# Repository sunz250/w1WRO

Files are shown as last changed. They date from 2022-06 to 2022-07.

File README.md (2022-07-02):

РРО: Будущие инженеры 2022 | LigaRobotov_OSError
====

В репозитории содержатся инженерные материалы, созданные и использованные командой OSError при проектировании и программировании беспилотного автомобиля для участия в Российской робототехнической олимпиаде 2022 в категории Будущие инженеры.

__https://youtu.be/0HV11u2FUfQ  - URL-адрес видеоролика на платформе youtube, показывающий автономное вождение автомобиля и его краткий обзор__

## Содержание

* `team_photo` - 2 командные фотографии: одна официальная и одна неофициальная (забавная) со всеми членами команды
* `robot_photo` - 6 фотографий транспортного средства (со всех сторон, сверху и снизу)
* `Видео` - файл video.md, в котором содержится URL-адрес на видеоролик на платформе youtube, показывающий автономное вождение автомобиля и демонстрацию его отдельных компонентов 
* `schematic`- схематические диаграммы всеx электромеханических компонентов (электронные компоненты и двигатели), используемых в автомобиле, и способы их соединения друг с другом
* `src` - программный код беспилотного автомобиля.
* `3D модели` - 3D модели для печати, необходимые для производства элементов автомобиля

## Описание робота

  Наш робот создан для решения задания РРО категории Будущие Инженеры. Его главной задачей является прохождение гоночной трассы с установленными на ней дорожными знаками или смещенными коридорами на время. Дорожные знаки указывают сторону полосы движения, по которой должен следовать автомобиль. Если на пути красный столб - нужно держаться правой стороны полосы. Если зелёный, то левой стороны полосы. Задание считается выполненным, если автомобиль проехал 3 круга. Сбивать или сдвигать с места дорожные знаки - запрещено. Направление, в котором автомобиль должен двигаться по трассе (по часовой стрелке или против часовой стрелки), будет варьироваться в разных матчах. Начальное положение автомобиля, а также количество и расположение дорожных знаков определяются случайным образом во время жеребьёвки перед матчем.

  Для движения интеллектуального беспилотного автомобиля используется мотор на 600 оборотов в минуту и потребляющий напряжение в 12 Вольт, соединенный с ведущей осью через дифференциал. Такая конструкция позволяет равномерно распределять крутящий момент мотора между ведущими колесами и обеспечивает надлежащую плавность хода. 
  
  Для ориентирования в процессе движения по гоночной трассе наш робот оборудован всеми необходимыми датчиками и сенсорами, а также камерой. Среди них - датчик абсолютной ориентации BNO085. В BNO085 есть свой модуль вычислений, это 32-битное ядро ARM Cortex M0, что позволяет производить большинство расчетов непосредственно внутри BNO085 и пользоваться уже готовыми результатами. Ядро получает данные: акселерометра, гироскопа, магнитометра, производит расчеты и сохраняет результаты. Результаты в дальнейшем могут быть запрошены внешними устройствами. 

  Для определения цвета дорожных знаков и ориентации используются 2 камеры, оснащенные сенсором SONY IMX-477, подключаются через интерфейс CSI.
  
  Главным вычислительным модулем на роботе является одноплатный вычислительный модуль NVIDIA Jetson Nano. Модуль Jetson Nano — это компактный компьютер на базе ИИ, который обладает производительностью и энергоэффективностью, необходимой для современных задач искусственного интеллекта, параллельной работы нескольких нейронных сетей и одновременной обработки данных с нескольких датчиков высокого разрешения. Поэтому он представляет собой отличное начальное решение для внедрения сложных средств искусственного интеллекта во встраиваемые системы. NVIDIA Jetson Nano обеспечивает потрясающие новые возможности в миллионах компактных энергоэффективных систем ИИ. Решение открывает новые возможности для встроенных IoT-приложений, в том числе для видеорегистраторов начального уровня, домашних роботов и интеллектуальных шлюзов с возможностями аналитики. 

## Описание алгоритма

  Для __квалификационного__ этапа соревнований используется программа cvalification.py. Стратегия прохождения данного этапа – движение вдоль внешней черной стены, используя показания BNO, те придерживаясь курса. После запуска программа инициализирует все необходимые модули, зажигается синий светодиод – робот готов к старту, необходимо лишь нажать кнопку. Далее робот набирает крейсерскую скорость и едет до ближайшей цветной линии. Если линия синего цвета – движение против часовой стрелки, если оранжевого – наоборот. Как только направление движения распознано, задается значение переменной clock: 1 по часовой и -1 против, она будет использоваться при расчете курса BNO. Далее движение продолжается до того, как робот увидит стену впереди себя, после чего требуемый курс BNO меняется на 90 градусов влево или вправо в зависимости от направления движения. Как только робот поворачивает, к счетчику секторов прибавляется 1. Так после 3х кругов, когда значение счетчика равно 12, робот останавливается.

  Для __финального__ этапа соревнований используется программа final.py. По большей части она аналогична cvalification.py, но также добавлено распознавание дорожных знаков. Старт, финиш и определение направление движения происходят как на квалификации. В поворотах объезд кубиков производится по пропорционально-дифференциальному регулятору, как только робот замечает кубик и определяет его цвет и позицию – начинается регуляция, причем различная в зависимости от положения знака. На прямых участках трассы регулирование реализовано иначе: используя метод векторов, робот рассчитывает угол отклонения знака от траектории движения, после чего рассчитывает ошибку в зависимости от цвета и положения кубика, своего положения, отклонения от курса, величины угла отклонения знака, которая корректирует курс BNO. Используя функциональную зависимость, калькулируется время маневра, после чего робот меняет свой курс, объезжая знак или приближаясь к нему, в конце маневра возвращаясь на исходную прямую траекторию. 

## Инструкция по сборке автомобиля

__1.	Начинаем с нижней рамы и крепления сервомотора__

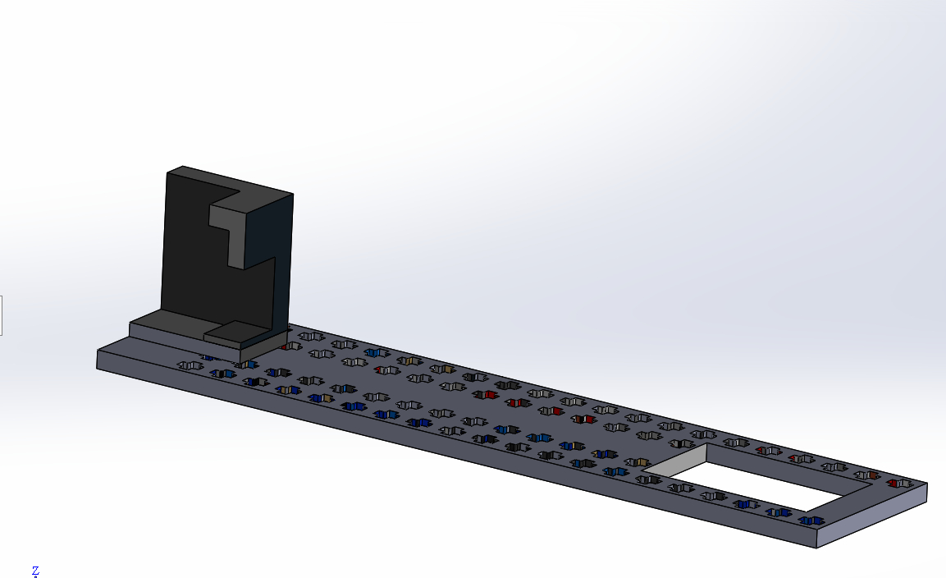
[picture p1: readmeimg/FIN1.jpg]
FIN1


__2.	Устанавливаем штифты и оси LEGO для крепления других элементов__

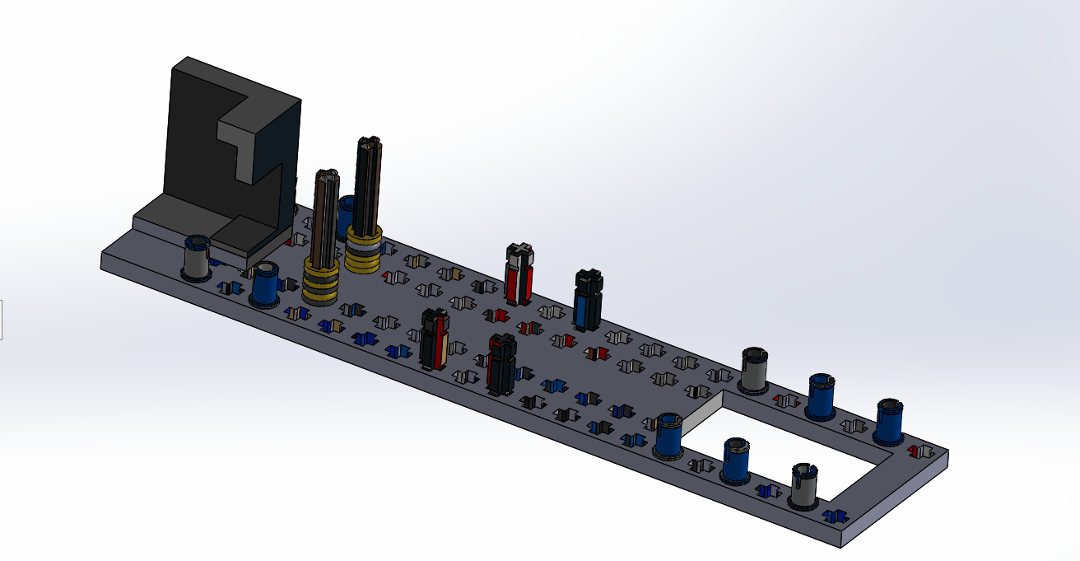
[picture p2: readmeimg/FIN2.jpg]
FIN2


__3.	Устанавливаем балки LEGO__

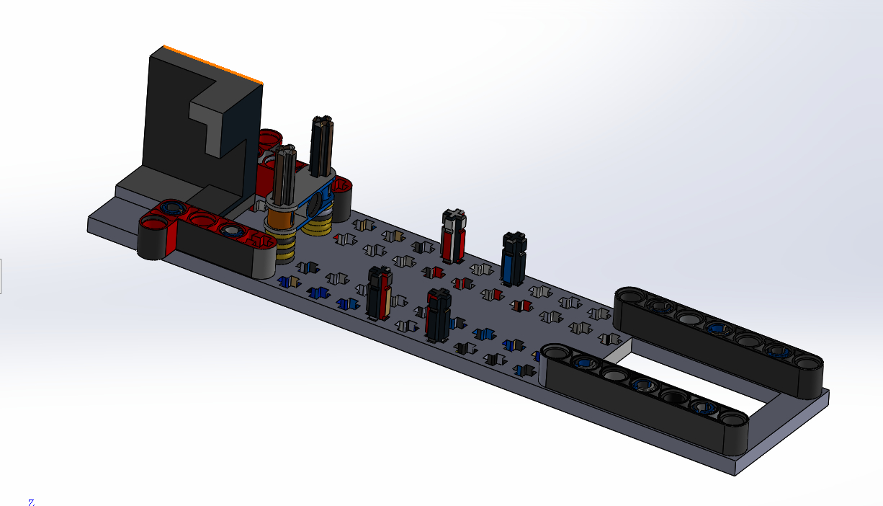
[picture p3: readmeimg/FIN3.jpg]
FIN3


__4.	Устанавливаем сервомотор__

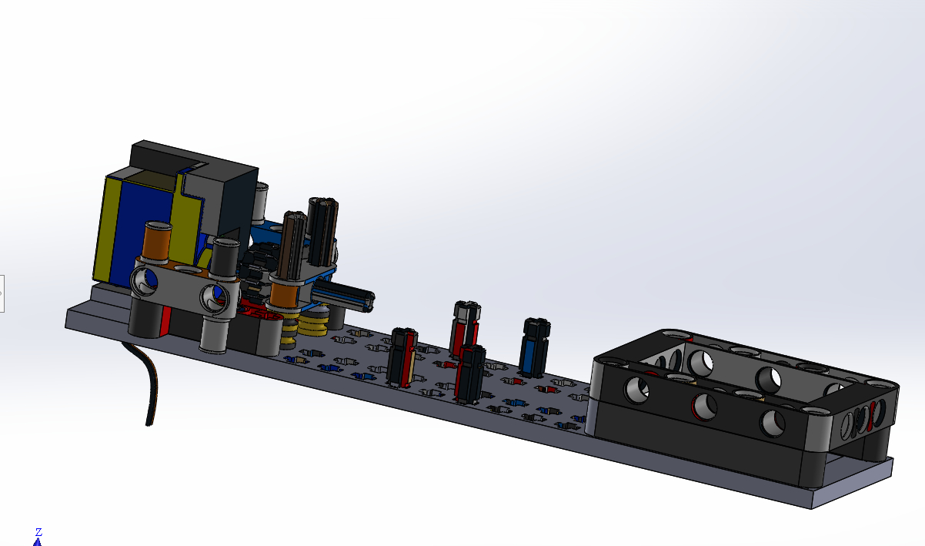
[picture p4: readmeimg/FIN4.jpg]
FIN4


__5.	Устанавливаем элементы рулевой рейки и дифференциал__

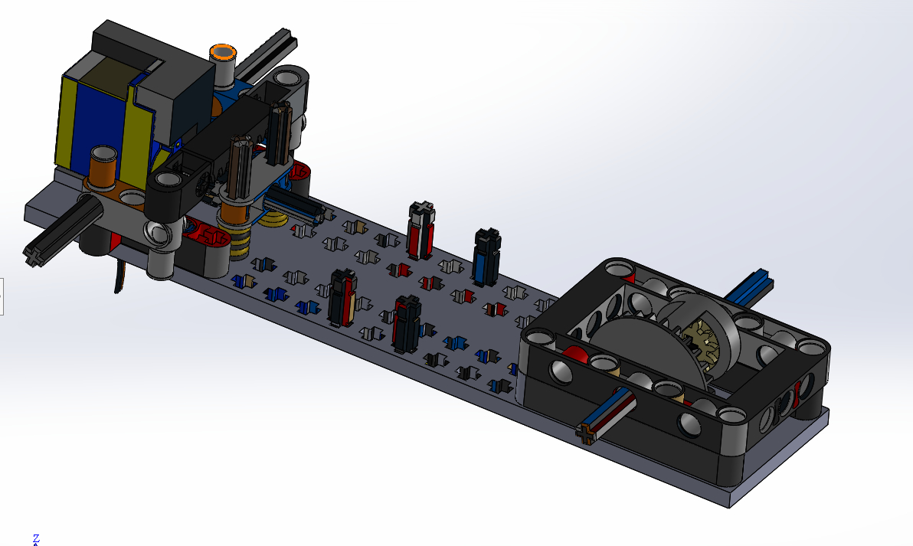
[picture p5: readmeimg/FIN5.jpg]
FIN5


__6.	Втыкаем LEGO штифты __

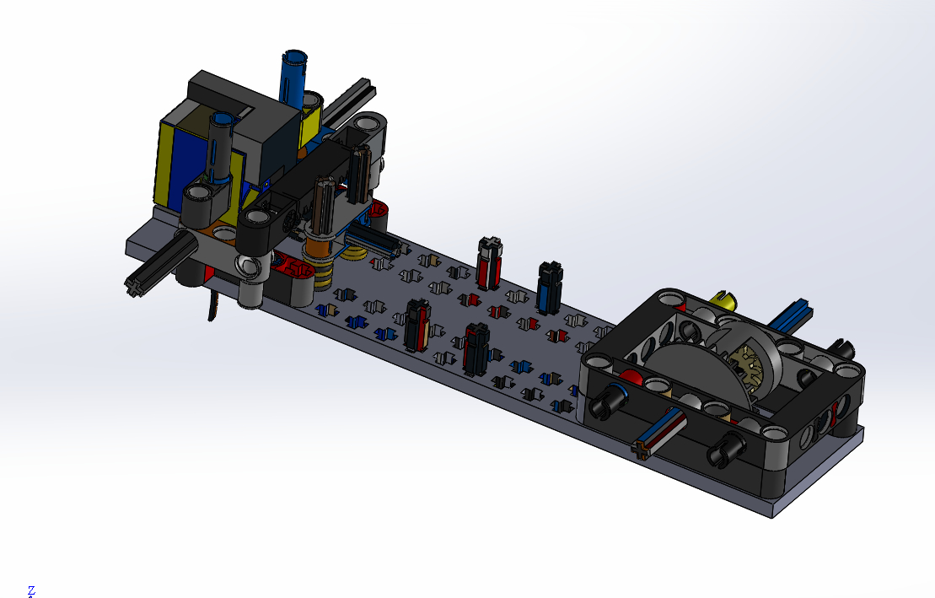
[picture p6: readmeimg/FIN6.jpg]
FIN6


__7.	Устанавливаем уголки и балки LEGO__

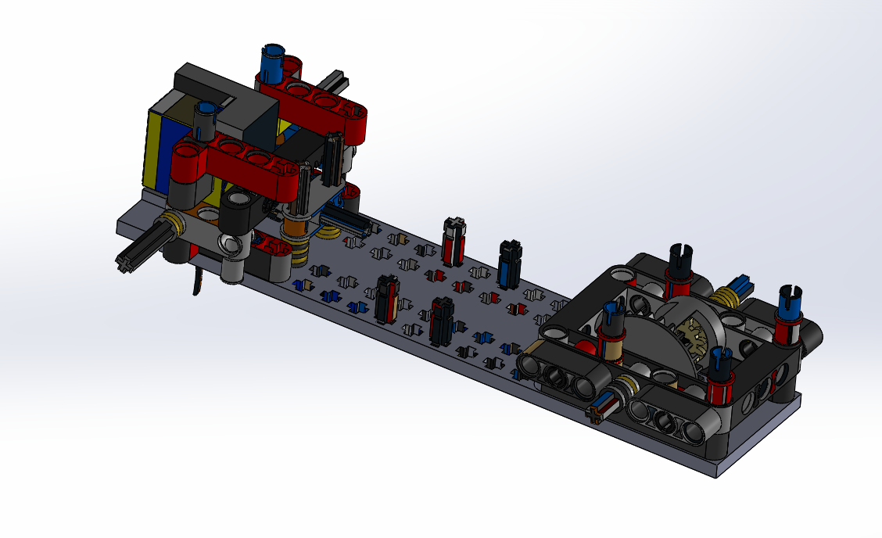
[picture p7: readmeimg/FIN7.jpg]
FIN7


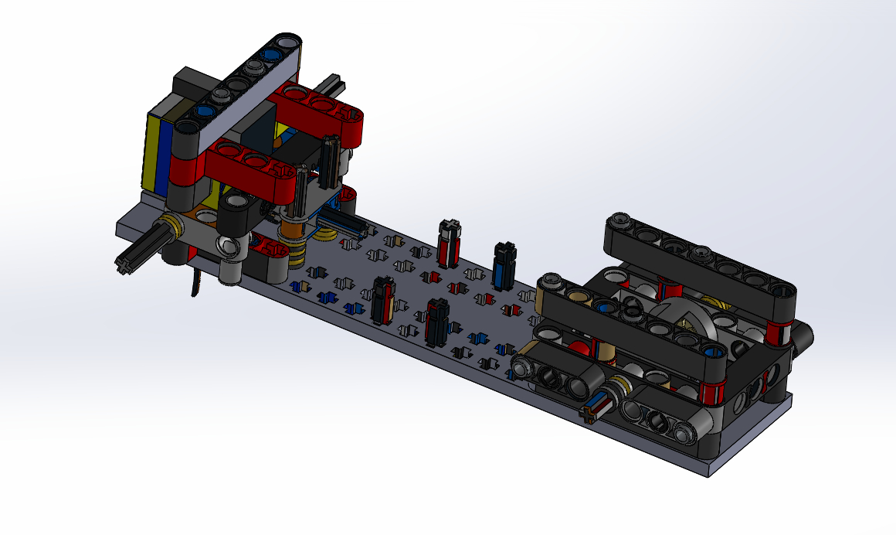
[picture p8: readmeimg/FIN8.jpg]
FIN8


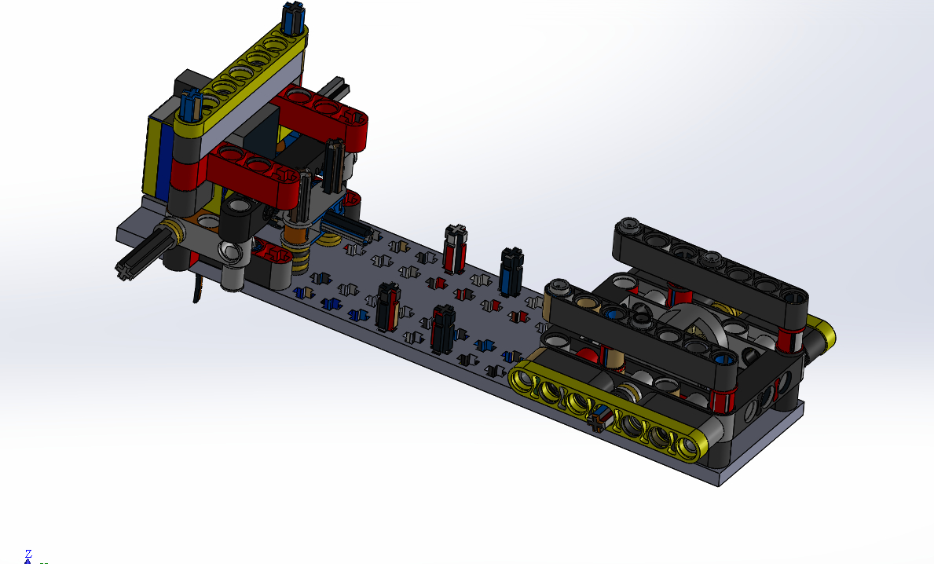
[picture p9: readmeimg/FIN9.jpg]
FIN9


__8.	Устанавливаем блок с мотором__

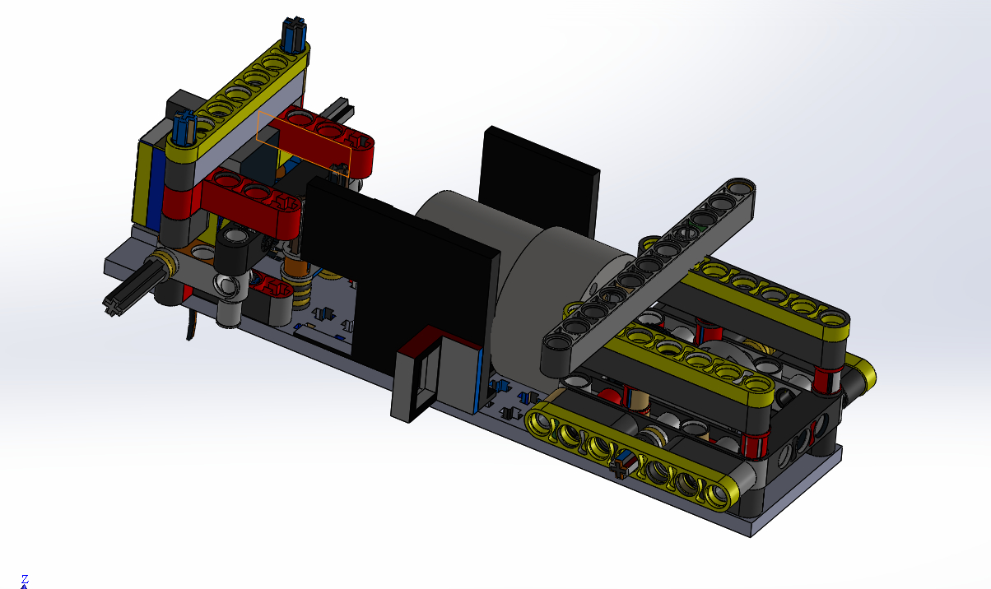
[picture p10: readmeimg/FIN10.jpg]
FIN10


__9.	Устанавливаем крепление JETSON NANO__

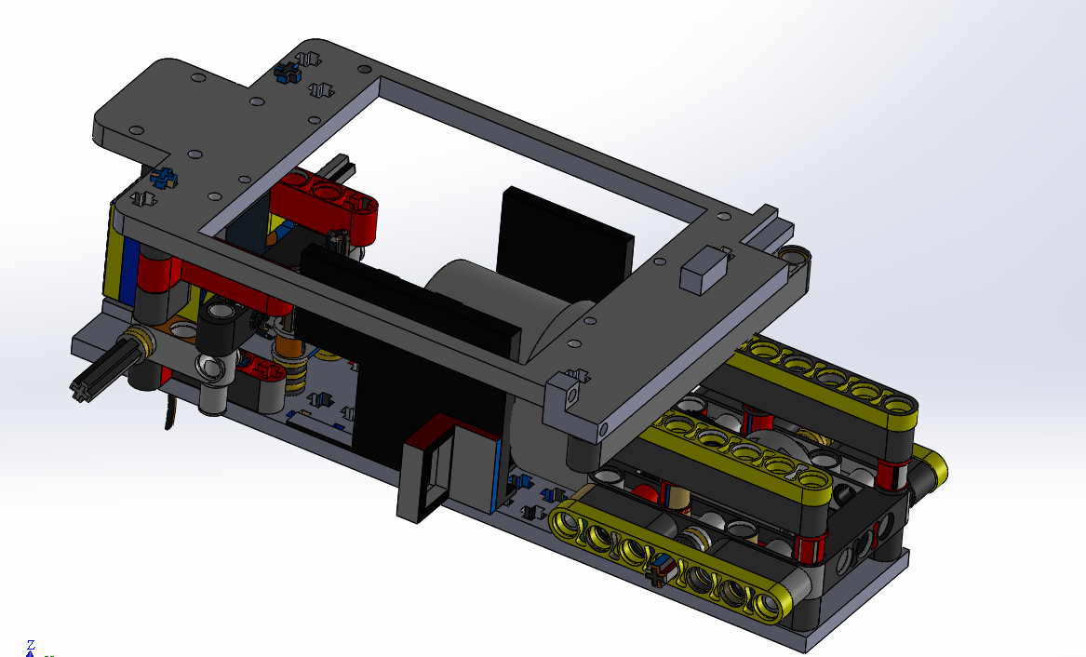
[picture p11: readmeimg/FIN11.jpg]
FIN11


__10.	Устанавливаем UPS POWER MODULE для JETSON NANO__

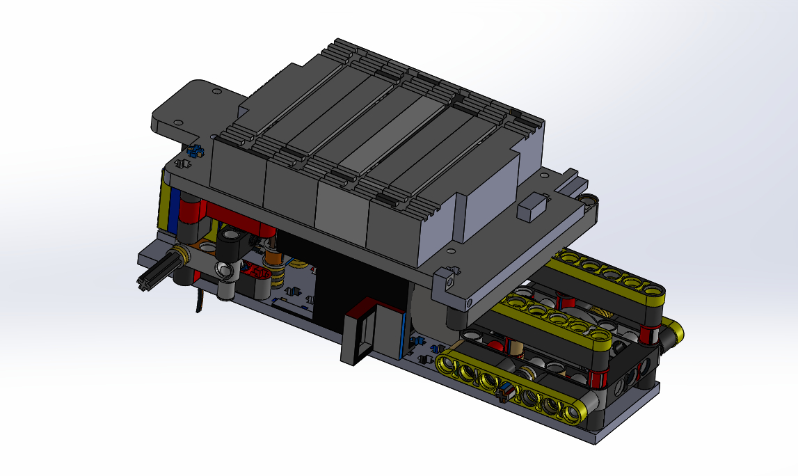
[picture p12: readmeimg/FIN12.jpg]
FIN12


__11.	Устанавливаем колеса__

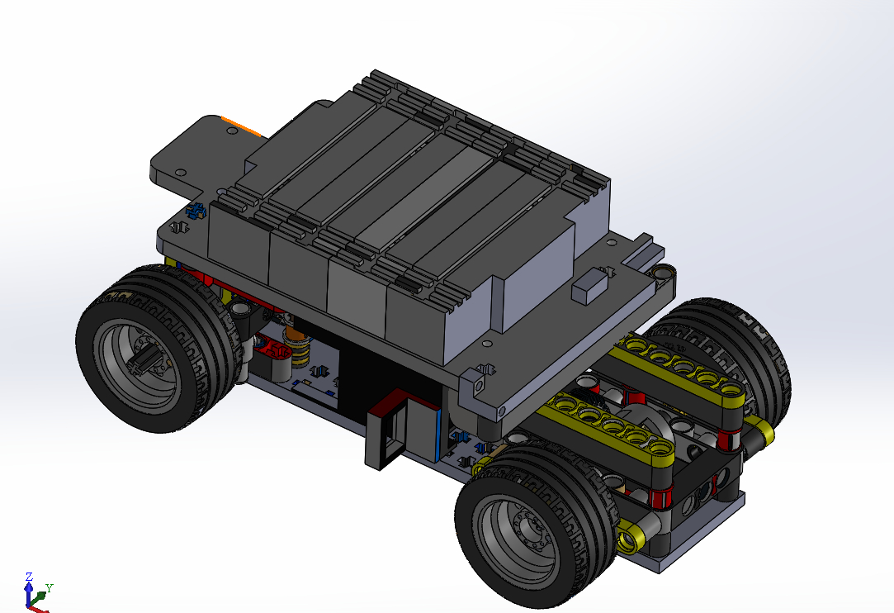
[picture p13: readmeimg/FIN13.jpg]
FIN13


__12.	Устанавливаем servo shield__

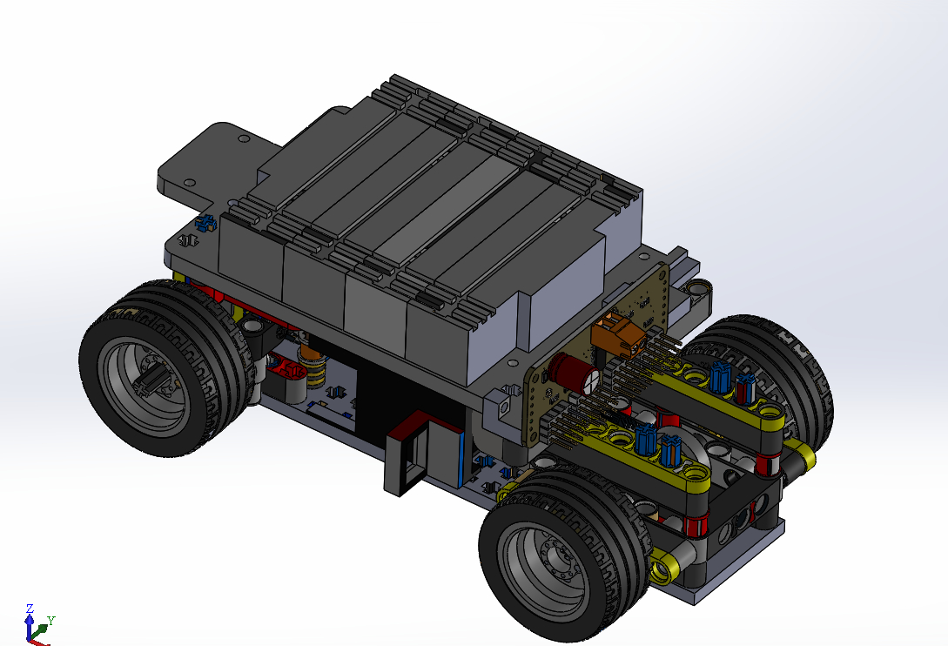
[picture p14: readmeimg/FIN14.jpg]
FIN14


__13.	Устанавливаем крепление камер и сами камеры, батарейный блок для мотора__

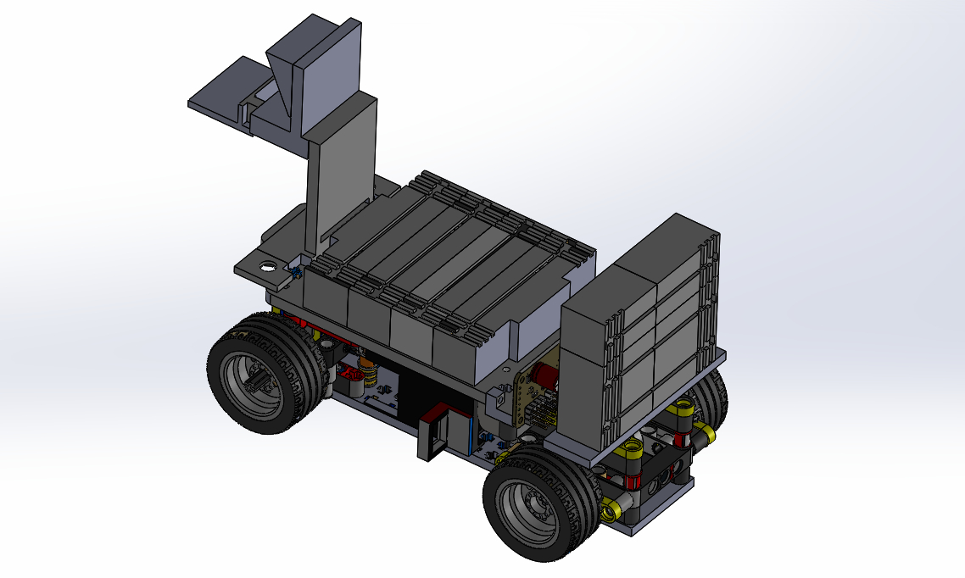
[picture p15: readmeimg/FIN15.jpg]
FIN15


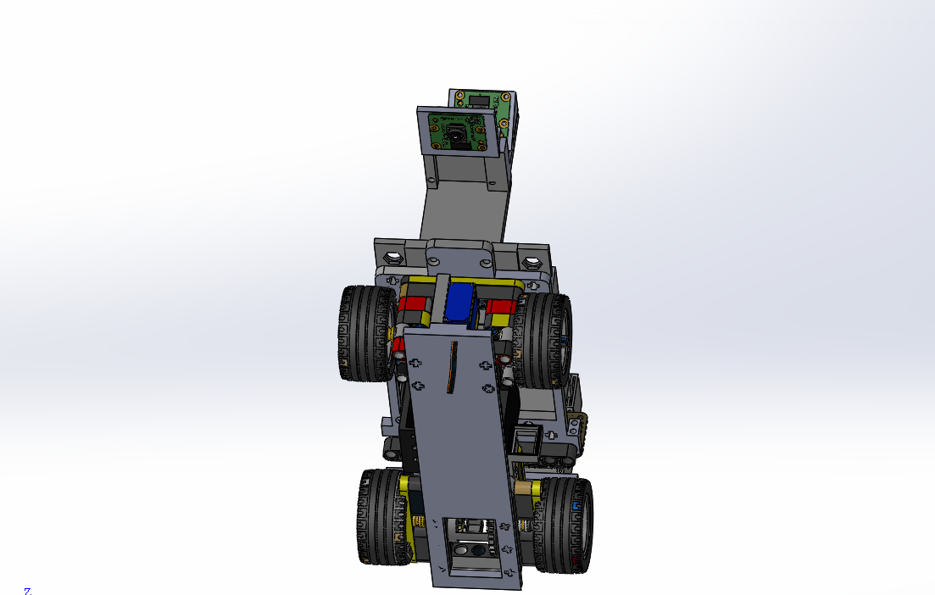
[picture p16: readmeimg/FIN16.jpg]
FIN16


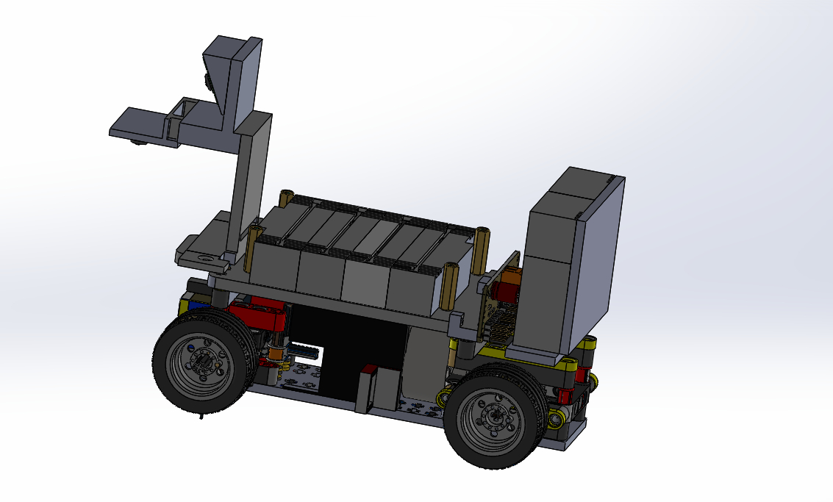
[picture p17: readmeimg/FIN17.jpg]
FIN17


__14.	Устанавливаем JETSON NANO, верхний блок с кнопкой, светодиодами, датчиком BNO085, DC-DC преобразователь для питания мотора, антенны (при необходимости). Сборка готова__

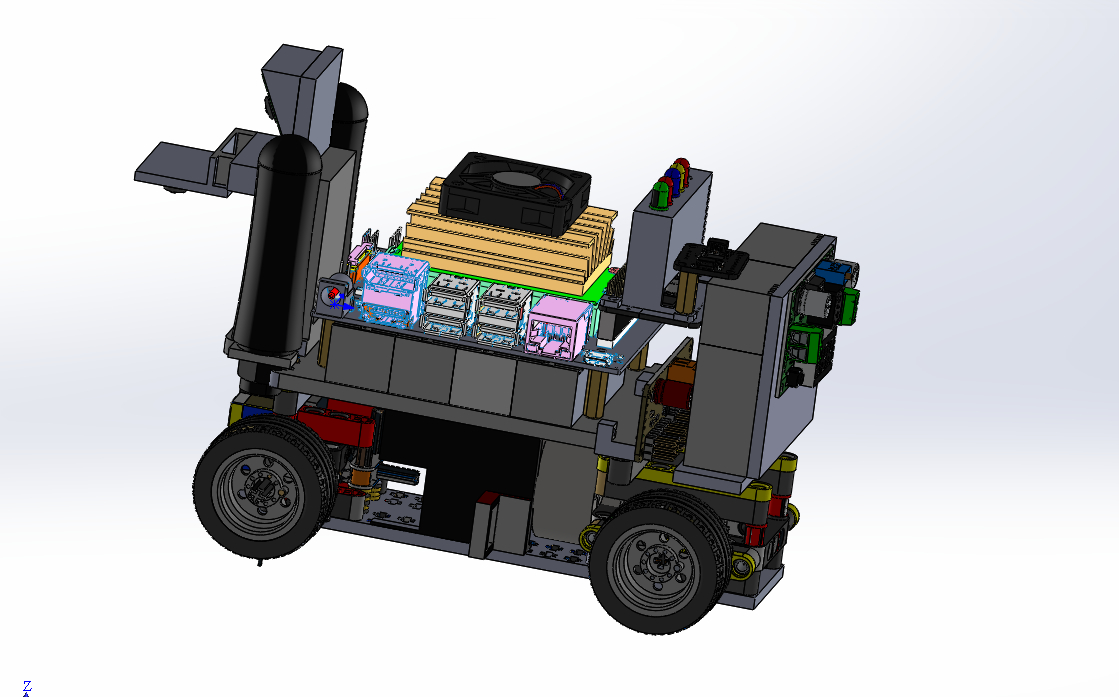
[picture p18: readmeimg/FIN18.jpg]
FIN18


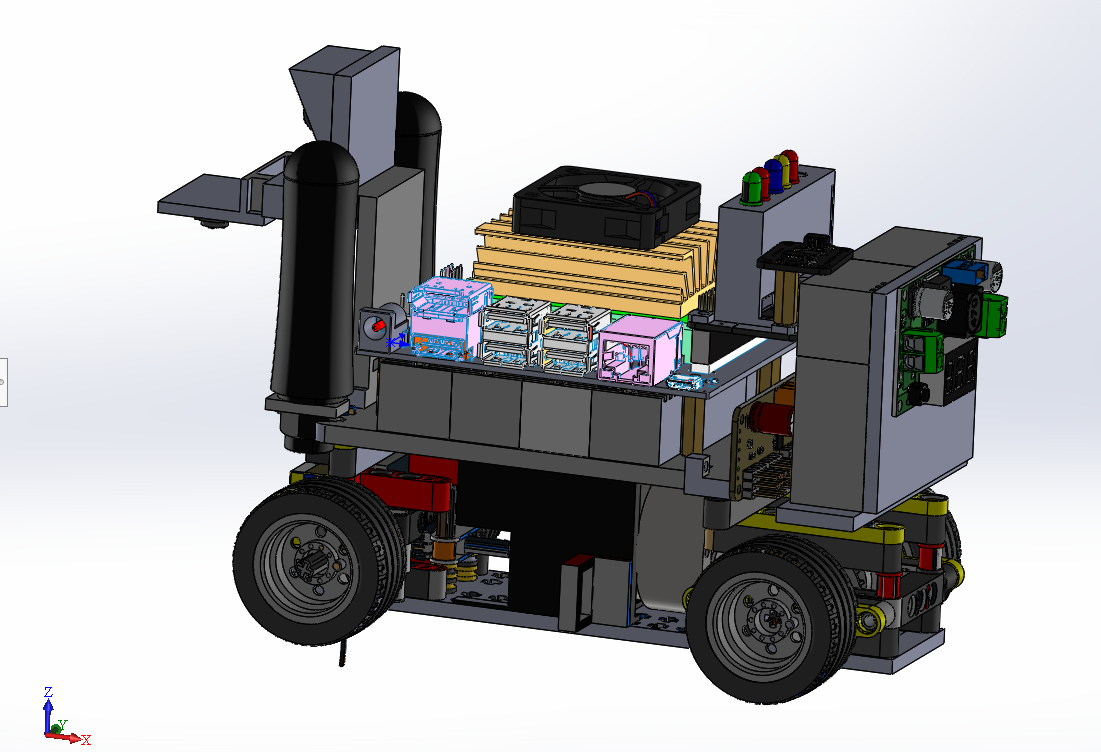
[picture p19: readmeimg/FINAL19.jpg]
FINAL19


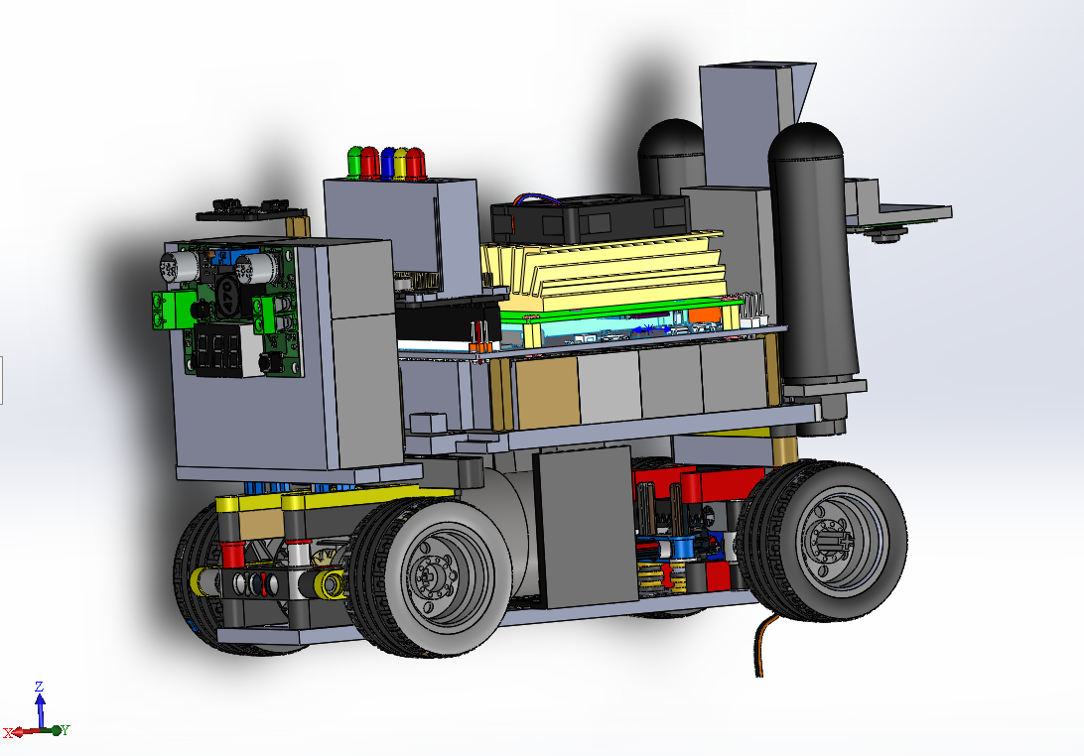
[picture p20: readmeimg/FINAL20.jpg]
FINAL20


## Подсоединение к роботу, загрузка и запуск программ

__1.	Включаем питание Jetson Nano и моторов, дожидаемся полной загрузки. Модуль стартует собственный hotspot с именем w1bot.__

__2.	Заранее скачиваем один из общедоступных IDE с поддержкой удаленного ssh подключения и редактирования кода, например мы используем Visual Studio Code.__

__3.	Выбираем из списка доступных сетей w1bot, подключаемся.__

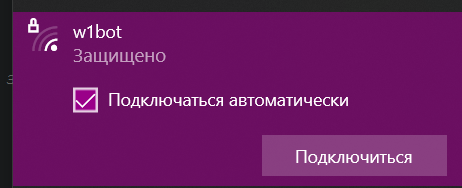
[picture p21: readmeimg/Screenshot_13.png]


__4.	После подключения переходим в каталог home/eg4/Documents/NN, находим папку competitions, в ней программы cvalification.py и final.py__

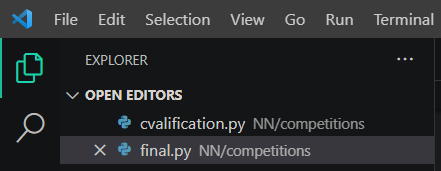
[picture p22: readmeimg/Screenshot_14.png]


__5.	Устанавливаем робота на полигоне, запускаем нужную программу, ждем, когда загорится синий светодиод, после чего робот готов к старту. Нажимаем на кнопку – происходит старт.__

__6.	При необходимости автозапуска: через консоль редактируем файл startpython.sh, расположенный в каталоге home/eg4. Там раскомментируем строчку с запуском программы, меняем имя на cvalification.py или final.py по необходимости. Таким образом после перезагрузки Jetson Nano программа запустится самостоятельно.__




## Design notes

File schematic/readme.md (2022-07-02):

Схематические диаграммы
====

* `Отдельные компоненты` - схематические диаграммы основного модуля NVIDIA Jetson Nano, датчика абсолютной ориентации BNO085, MOTOR и SERVO шилдов, а также UPS POWER MODULE
* `Электрическая схема` - схема, иллюстрирующая все электрические компоненты, используемые в автомобиле, и способы их соединения друг с другом
* `Механическая схема` - схема, иллюстрирующая все механические компоненты, используемые в автомобиле, и способы их соединения друг с другом

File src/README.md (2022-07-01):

Программный код
====

* `cvalification.py` - программа для квалификационного раунда
* `final.py` - программа для финального раунда

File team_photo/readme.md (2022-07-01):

Командные фото
====
* `official.jpg` - официальная фотография команды
* `fun.jpg` - неофициальная (забавная) фотография команды

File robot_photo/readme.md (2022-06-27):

Фото автомобиля
====

* `вид_сверху.jpg | вид_сзади.jpg | вид_слева.jpg | вид_снизу.jpg | вид_спереди.jpg | вид_справа.jpg` - 6 фотографий транспортного средства (со всех сторон, сверху и снизу)
* `high_quality_pics.zip` - zip. архив, содержащий те же 6 фотографий в наилучшем качестве

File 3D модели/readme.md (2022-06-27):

3D Модели
====
Здесь представлены 3D модели для печати, необходимые для производства элементов автомобиля. Из полученного набора элементов можно собрать искомый автомобиль. Каждый из элементов автомобиля был изготовлен во множестве экземпляров и не раз протестирован в полевых условиях. Ведется постоянная доработка элеметов.

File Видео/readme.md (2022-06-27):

Видео
====

* `video.md` - в файле содержится URL-адрес на видеоролик на платформе youtube, показывающий автономное вождение автомобиля и демонстрацию его составных компонентов

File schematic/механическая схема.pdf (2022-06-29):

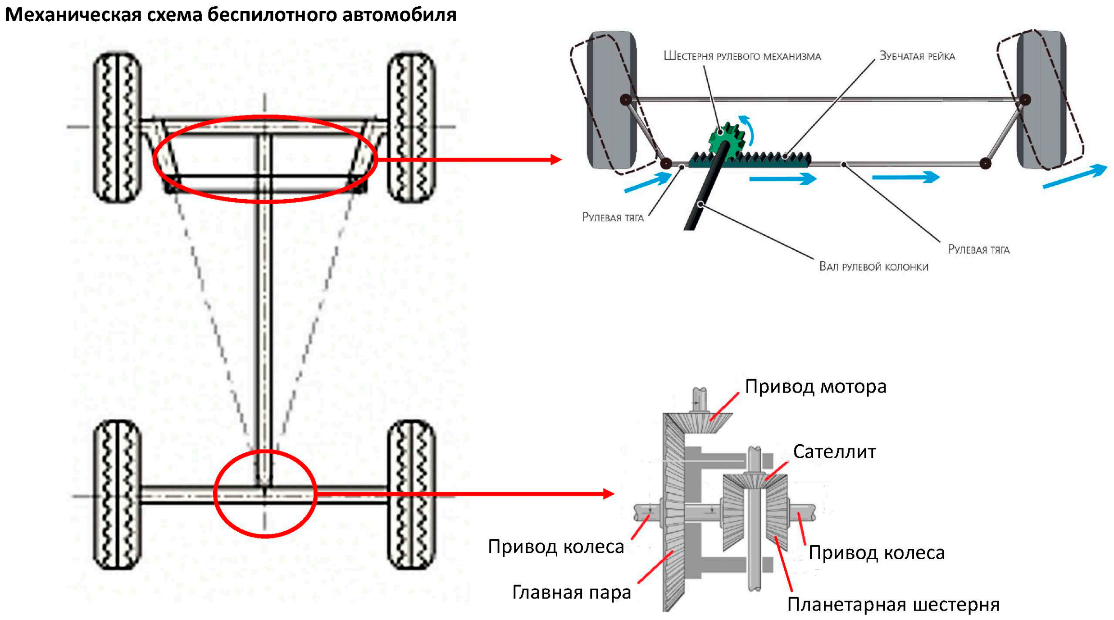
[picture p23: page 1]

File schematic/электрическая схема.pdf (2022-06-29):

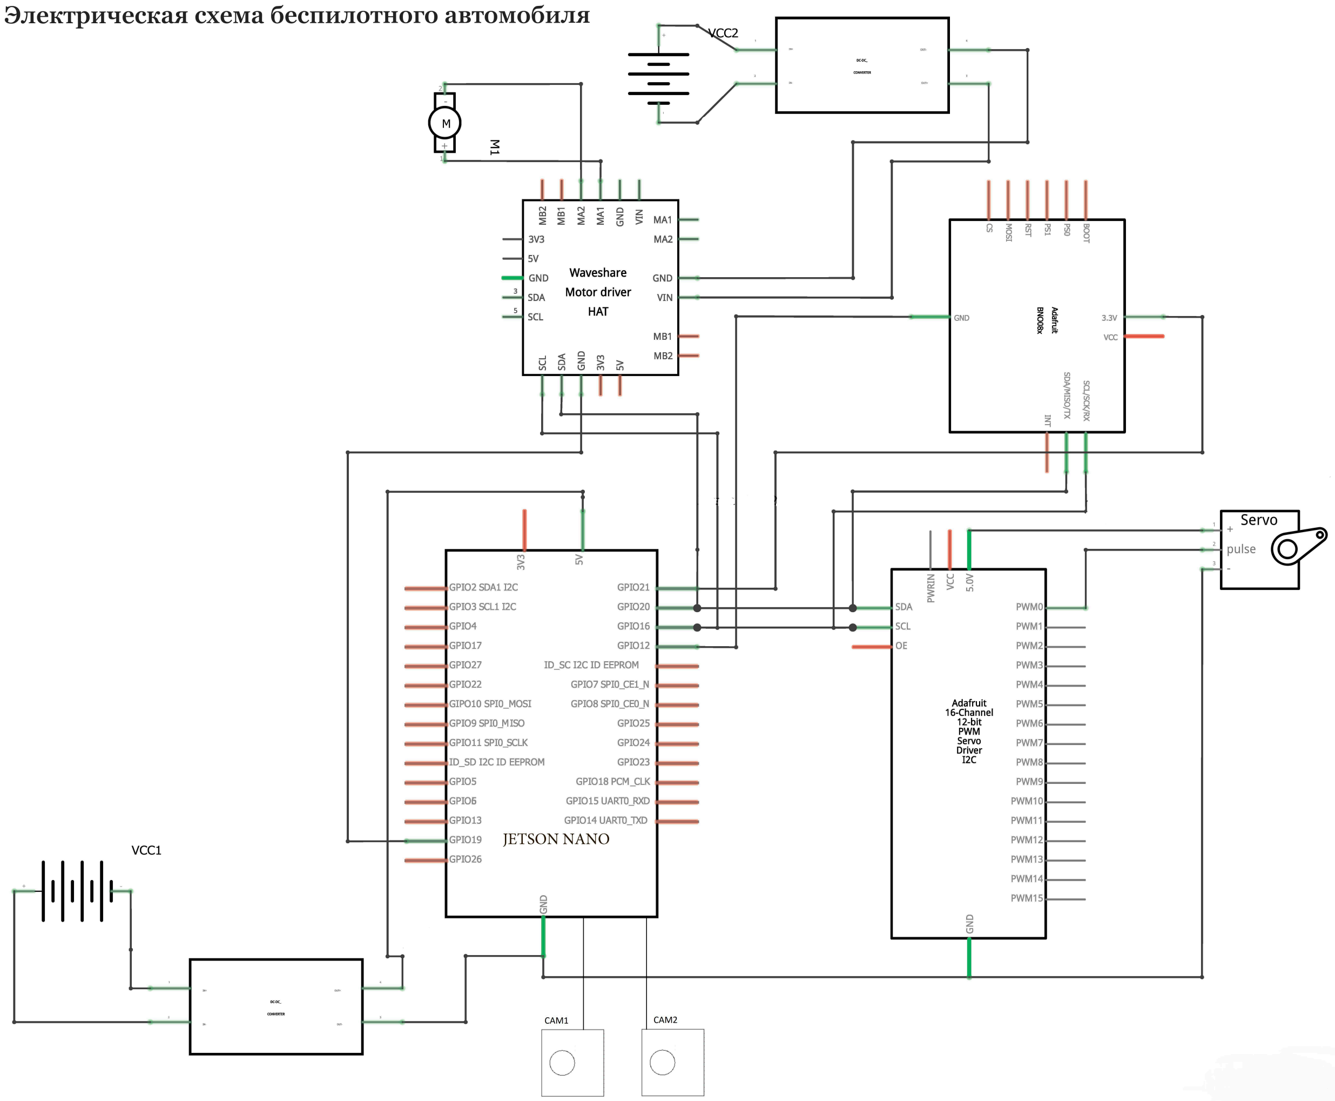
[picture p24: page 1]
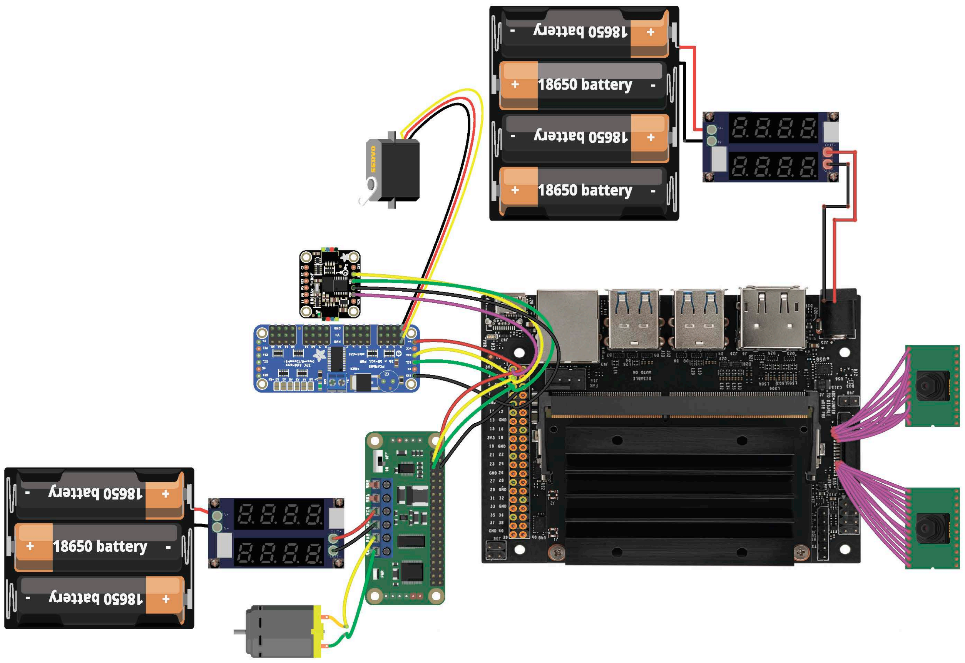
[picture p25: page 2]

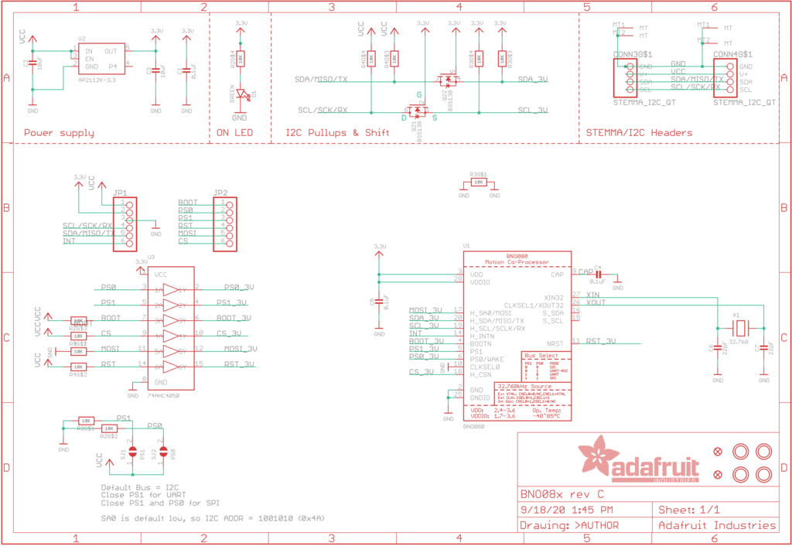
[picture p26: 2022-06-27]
schematic/отдельные компоненты/BNO085_Schematics.png

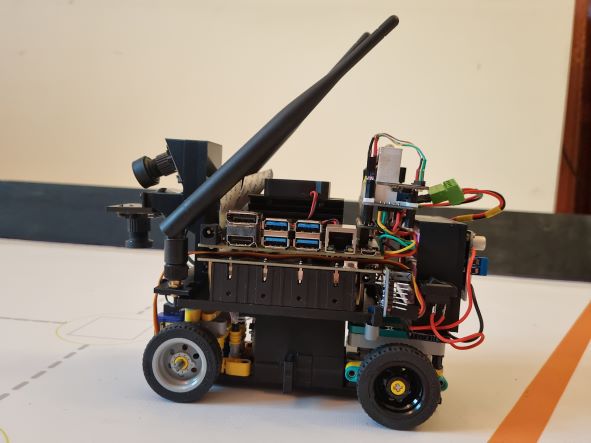
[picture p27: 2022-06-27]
robot_photo/вид_слева.jpg

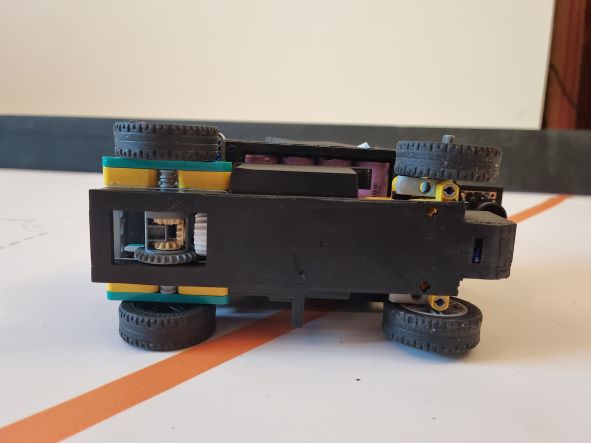
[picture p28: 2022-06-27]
robot_photo/вид_снизу.jpg

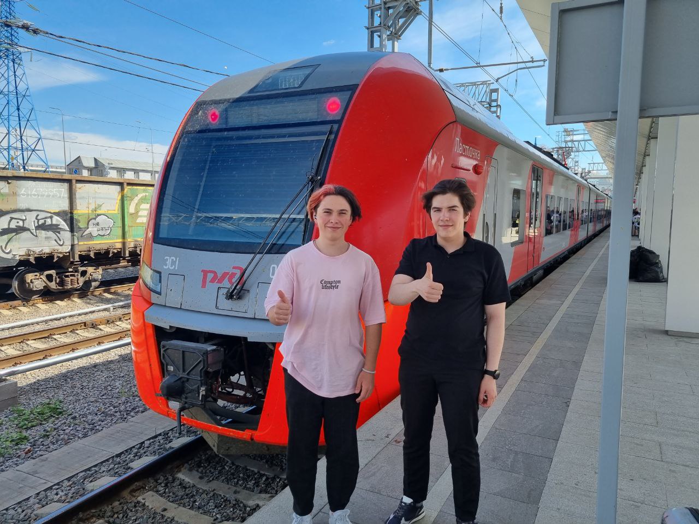
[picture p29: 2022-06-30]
team_photo/fun.jpg

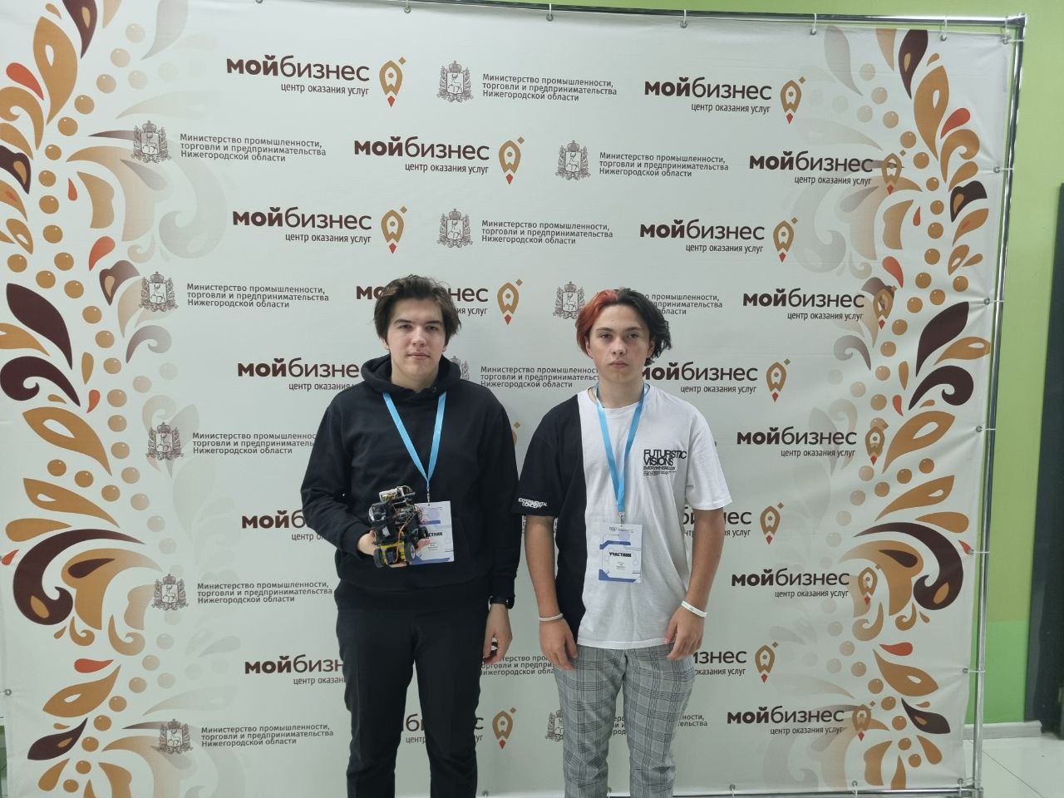
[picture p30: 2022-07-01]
team_photo/official.jpg

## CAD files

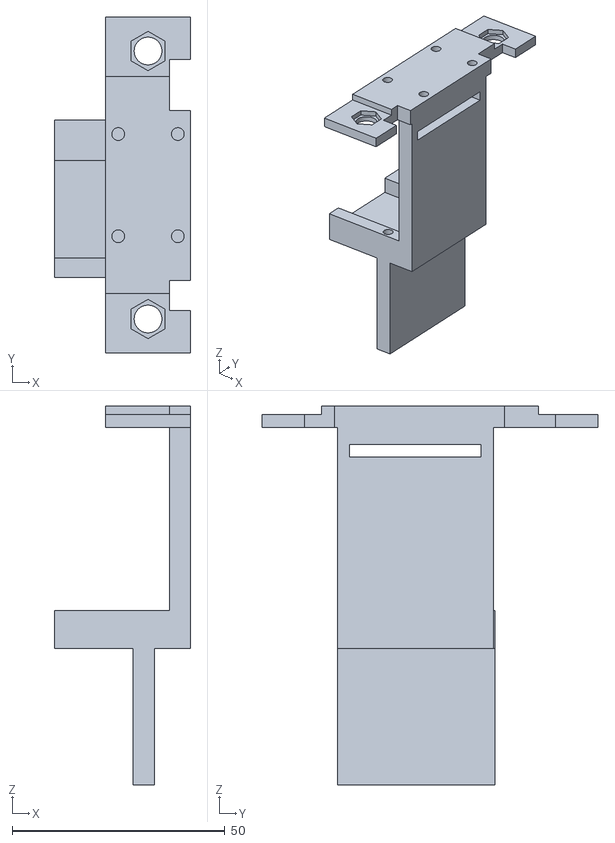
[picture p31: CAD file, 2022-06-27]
3D модели/крепление камер и антенн.STL
32.0 x 78.9 x 89.0

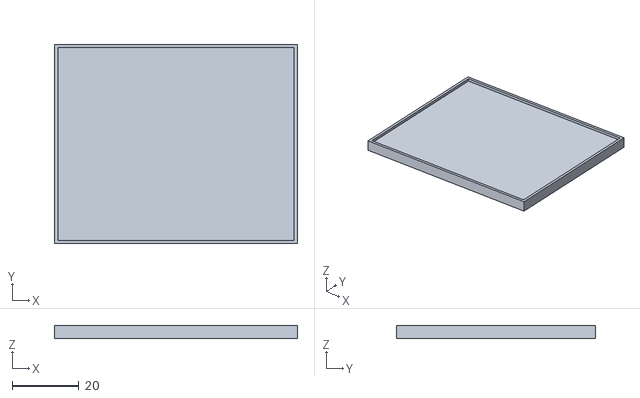
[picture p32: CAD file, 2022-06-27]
3D модели/крышка бат. блока.STL
73.0 x 59.9 x 4.00

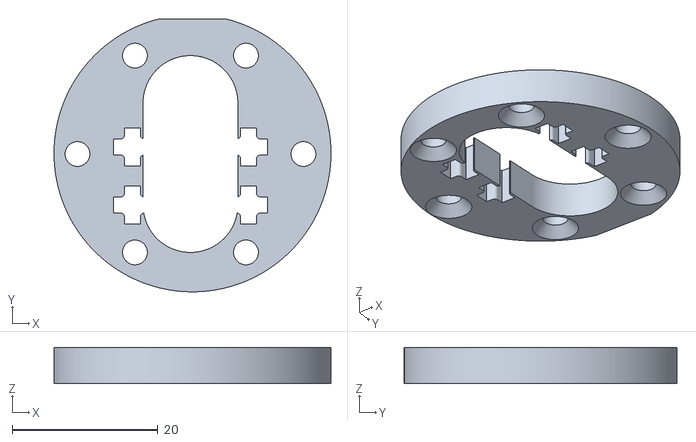
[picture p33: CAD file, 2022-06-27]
3D модели/крепление мотора.STL
38.0 x 37.4 x 5.00

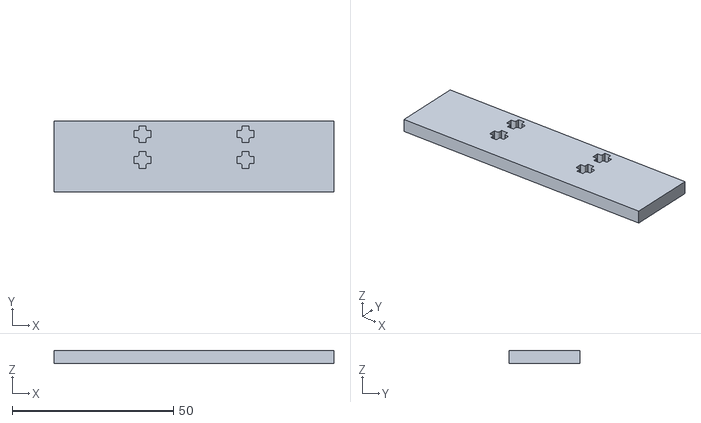
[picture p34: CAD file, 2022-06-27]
3D модели/переход на Lego.STL
86.7 x 21.8 x 4.00

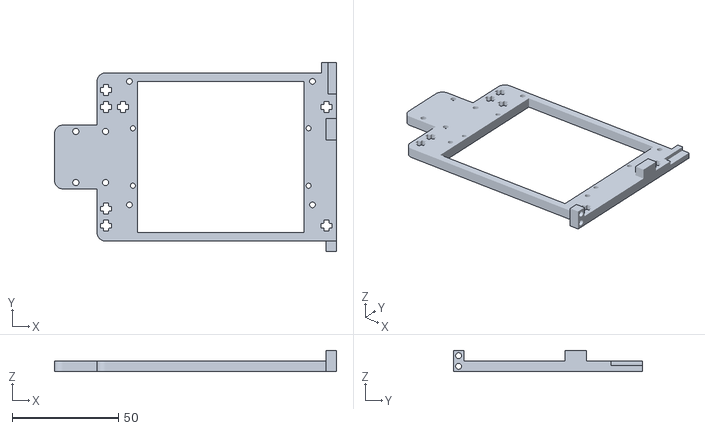
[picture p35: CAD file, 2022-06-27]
3D модели/крепление Jetson.STL
132.5 x 89.0 x 10.0

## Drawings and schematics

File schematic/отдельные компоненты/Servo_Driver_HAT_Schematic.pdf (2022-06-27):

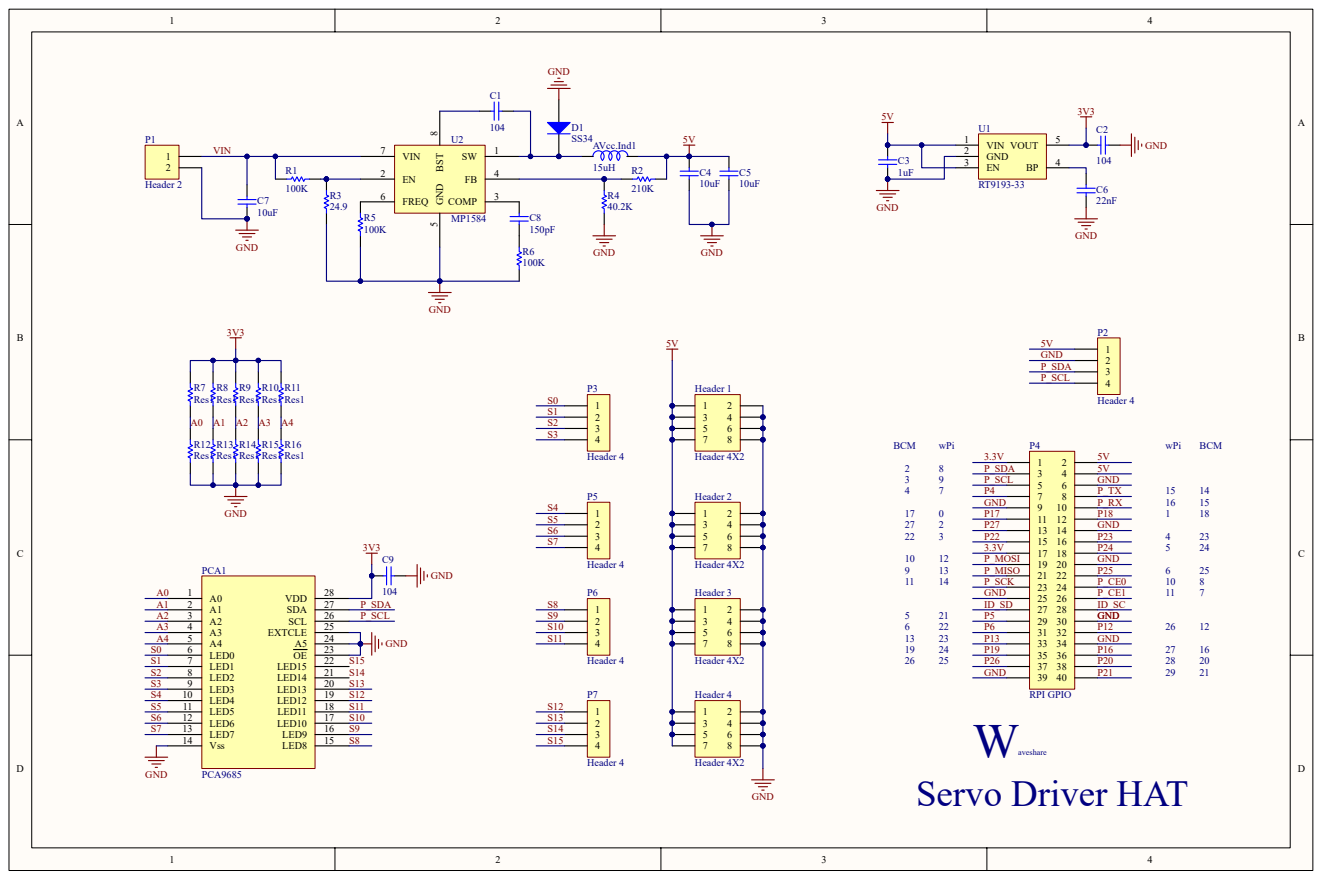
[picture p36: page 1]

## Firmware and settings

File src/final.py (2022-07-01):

# импортируем необходимые библиотеки для вычислений
import time
import numpy as np
import jetson.inference
import jetson.utils
import cv2
import board
import digitalio
import smbus
from threading import Thread

# задаем необхыдимы константы и классы для измерения заряда батареи

# Config Register (R/W)
_REG_CONFIG                 = 0x00
# SHUNT VOLTAGE REGISTER (R)
_REG_SHUNTVOLTAGE           = 0x01

# BUS VOLTAGE REGISTER (R)
_REG_BUSVOLTAGE             = 0x02

# POWER REGISTER (R)
_REG_POWER                  = 0x03

# CURRENT REGISTER (R)
_REG_CURRENT                = 0x04

# CALIBRATION REGISTER (R/W)
_REG_CALIBRATION            = 0x05

class BusVoltageRange:
    """Constants for ``bus_voltage_range``"""
    RANGE_16V               = 0x00      # set bus voltage range to 16V
    RANGE_32V               = 0x01      # set bus voltage range to 32V (default)

class Gain:
    """Constants for ``gain``"""
    DIV_1_40MV              = 0x00      # shunt prog. gain set to  1, 40 mV range
    DIV_2_80MV              = 0x01      # shunt prog. gain set to /2, 80 mV range
    DIV_4_160MV             = 0x02      # shunt prog. gain set to /4, 160 mV range
    DIV_8_320MV             = 0x03      # shunt prog. gain set to /8, 320 mV range

class ADCResolution:
    """Constants for ``bus_adc_resolution`` or ``shunt_adc_resolution``"""
    ADCRES_9BIT_1S          = 0x00      #  9bit,   1 sample,     84us
    ADCRES_10BIT_1S         = 0x01      # 10bit,   1 sample,    148us
    ADCRES_11BIT_1S         = 0x02      # 11 bit,  1 sample,    276us
    ADCRES_12BIT_1S         = 0x03      # 12 bit,  1 sample,    532us
    ADCRES_12BIT_2S         = 0x09      # 12 bit,  2 samples,  1.06ms
    ADCRES_12BIT_4S         = 0x0A      # 12 bit,  4 samples,  2.13ms
    ADCRES_12BIT_8S         = 0x0B      # 12bit,   8 samples,  4.26ms
    ADCRES_12BIT_16S        = 0x0C      # 12bit,  16 samples,  8.51ms
    ADCRES_12BIT_32S        = 0x0D      # 12bit,  32 samples, 17.02ms
    ADCRES_12BIT_64S        = 0x0E      # 12bit,  64 samples, 34.05ms
    ADCRES_12BIT_128S       = 0x0F      # 12bit, 128 samples, 68.10ms

class Mode:
    """Constants for ``mode``"""
    POWERDOW                = 0x00      # power down
    SVOLT_TRIGGERED         = 0x01      # shunt voltage triggered
    BVOLT_TRIGGERED         = 0x02      # bus voltage triggered
    SANDBVOLT_TRIGGERED     = 0x03      # shunt and bus voltage triggered
    ADCOFF                  = 0x04      # ADC off
    SVOLT_CONTINUOUS        = 0x05      # shunt voltage continuous
    BVOLT_CONTINUOUS        = 0x06      # bus voltage continuous
    SANDBVOLT_CONTINUOUS    = 0x07      # shunt and bus voltage continuous


class INA219:
    def __init__(self, i2c_bus=1, addr=0x40):
        self.bus = smbus.SMBus(i2c_bus);
        self.addr = addr

        # Set chip to known config values to start
        self._cal_value = 0
        self._current_lsb = 0
        self._power_lsb = 0
        self.set_calibration_32V_2A()

    def read(self,address):
        data = self.bus.read_i2c_block_data(self.addr, address, 2)
        return ((data[0] * 256 ) + data[1])

    def write(self,address,data):
        temp = [0,0]
        temp[1] = data & 0xFF
        temp[0] =(data & 0xFF00) >> 8
        self.bus.write_i2c_block_data(self.addr,address,temp)

    def set_calibration_32V_2A(self):
        """Configures to INA219 to be able to measure up to 32V and 2A of current. Counter
           overflow occurs at 3.2A.
           ..note :: These calculations assume a 0.1 shunt ohm resistor is present
        """
        # By default we use a pretty huge range for the input voltage,
        # which probably isn't the most appropriate choice for system
        # that don't use a lot of power.  But all of the calculations
        # are shown below if you want to change the settings.  You will
        # also need to change any relevant register settings, such as
        # setting the VBUS_MAX to 16V instead of 32V, etc.

        # VBUS_MAX = 32V             (Assumes 32V, can also be set to 16V)
        # VSHUNT_MAX = 0.32          (Assumes Gain 8, 320mV, can also be 0.16, 0.08, 0.04)
        # RSHUNT = 0.1               (Resistor value in ohms)

        # 1. Determine max possible current
        # MaxPossible_I = VSHUNT_MAX / RSHUNT
        # MaxPossible_I = 3.2A

        # 2. Determine max expected current
        # MaxExpected_I = 2.0A

        # 3. Calculate possible range of LSBs (Min = 15-bit, Max = 12-bit)
        # MinimumLSB = MaxExpected_I/32767
        # MinimumLSB = 0.000061              (61uA per bit)
        # MaximumLSB = MaxExpected_I/4096
        # MaximumLSB = 0,000488              (488uA per bit)

        # 4. Choose an LSB between the min and max values
        #    (Preferrably a roundish number close to MinLSB)
        # CurrentLSB = 0.0001 (100uA per bit)
        self._current_lsb = .1  # Current LSB = 100uA per bit

        # 5. Compute the calibration register
        # Cal = trunc (0.04096 / (Current_LSB * RSHUNT))
        # Cal = 4096 (0x1000)

        self._cal_value = 4096

        # 6. Calculate the power LSB
        # PowerLSB = 20 * CurrentLSB
        # PowerLSB = 0.002 (2mW per bit)
        self._power_lsb = .002  # Power LSB = 2mW per bit

        self.write(_REG_CALIBRATION,self._cal_value)

        self.bus_voltage_range = BusVoltageRange.RANGE_32V
        self.gain = Gain.DIV_8_320MV
        self.bus_adc_resolution = ADCResolution.ADCRES_12BIT_32S
        self.shunt_adc_resolution = ADCResolution.ADCRES_12BIT_32S
        self.mode = Mode.SANDBVOLT_CONTINUOUS
        self.config = self.bus_voltage_range << 13 | \
                      self.gain << 11 | \
                      self.bus_adc_resolution << 7 | \
                      self.shunt_adc_resolution << 3 | \
                      self.mode
        self.write(_REG_CONFIG,self.config)

    def getShuntVoltage_mV(self):
        self.write(_REG_CALIBRATION,self._cal_value)
        value = self.read(_REG_SHUNTVOLTAGE)
        if value > 32767:
            value -= 65535
        return value * 0.01

    def getBusVoltage_V(self):
        self.write(_REG_CALIBRATION,self._cal_value)
        self.read(_REG_BUSVOLTAGE)
        return (self.read(_REG_BUSVOLTAGE) >> 3) * 0.004

    def getCurrent_mA(self):
        value = self.read(_REG_CURRENT)
        if value > 32767:
            value -= 65535
        return value * self._current_lsb

    def getPower_W(self):
        self.write(_REG_CALIBRATION,self._cal_value)
        value = self.read(_REG_POWER)
        if value > 32767:
            value -= 65535
        return value * self._power_lsb
        
ina219 = INA219(addr=0x42)

# инициализируем светодиоды и кнопку на верхней панели

redcubled = digitalio.DigitalInOut(board.D26) 
greencubled = digitalio.DigitalInOut(board.D20) 


redcubled.direction = digitalio.Direction.OUTPUT
greencubled.direction = digitalio.Direction.OUTPUT

redled = digitalio.DigitalInOut(board.D13)
redled.direction = digitalio.Direction.OUTPUT

whiteled = digitalio.DigitalInOut(board.D12)
whiteled.direction = digitalio.Direction.OUTPUT

greenled = digitalio.DigitalInOut(board.D12)
greenled.direction = digitalio.Direction.OUTPUT

blueled = digitalio.DigitalInOut(board.D11)
blueled.direction = digitalio.Direction.OUTPUT

button = digitalio.DigitalInOut(board.D22)
button.direction = digitalio.Direction.INPUT

# импортируем необходимые библиотеки для управления мотором и сервомотором

from adafruit_motorkit import MotorKit
kit = MotorKit(i2c=board.I2C())
from adafruit_servokit import ServoKit
servokit = ServoKit(channels=8)

# импортируем модули для BNO085

from math import atan2, sqrt, pi
from board import SCL, SDA
from busio import I2C
from adafruit_bno08x import (
    BNO_REPORT_STEP_COUNTER,
    BNO_REPORT_ROTATION_VECTOR,
    BNO_REPORT_GEOMAGNETIC_ROTATION_VECTOR,
)
from adafruit_bno08x.i2c import BNO08X_I2C

i2c = I2C(SCL, SDA, frequency=800000 )
bno = BNO08X_I2C(i2c , address=0x4A)

bno.enable_feature(BNO_REPORT_STEP_COUNTER)
bno.enable_feature(BNO_REPORT_ROTATION_VECTOR)
bno.enable_feature(BNO_REPORT_GEOMAGNETIC_ROTATION_VECTOR)

start_heading = 0

# функция поиска угла

def find_heading(dqw, dqx, dqy, dqz):
    norm = sqrt(dqw * dqw + dqx * dqx + dqy * dqy + dqz * dqz)
    dqw = dqw / norm
    dqx = dqx / norm
    dqy = dqy / norm
    dqz = dqz / norm

    ysqr = dqy * dqy

    t3 = +2.0 * (dqw * dqz + dqx * dqy)
    t4 = +1.0 - 2.0 * (ysqr + dqz * dqz)
    yaw_raw = atan2(t3, t4)
    yaw = yaw_raw * 180.0 / pi
    if yaw > 0:
        yaw = 360 - yaw
    else:
        yaw = abs(yaw)
    return ((360+yaw-start_heading)%360)      # heading in 360 clockwise

quat_i, quat_j, quat_k, quat_real = bno.quaternion
start_heading = find_heading(quat_real, quat_i, quat_j, quat_k)

# class для взаимодействия с BNO085

class BNO085:
    global bno,i2c,img
    def __init__(self):
        
        (self.quat_i, self.quat_j, self.quat_k, self.quat_real)=bno.quaternion
        self.heading = find_heading(self.quat_real, self.quat_i, self.quat_j, self.quat_k)
        self.stopped=False
    def start(self):
        Thread(target=self.update,args=()).start()
        return self
    def update(self):
        while True:
            if self.stopped:
                return
            (self.quat_i, self.quat_j, self.quat_k, self.quat_real)=bno.quaternion
            self.heading = float(find_heading(self.quat_real, self.quat_i, self.quat_j, self.quat_k))
            self.heading=int((self.heading+45)%360) #45
    def read(self):
        return self.heading
    def stop(self):
        self.stopped=True

# инициализируем камеры и доп. модули

camera = jetson.utils.videoSource("csi://0", argv=['--input-flip=rotate-0', '--input-width=640', '--input-height=480', '--input-rate=60'])
camera_line = jetson.utils.videoSource("csi://1", argv=['--input-flip=rotate-0', '--input-width=640', '--input-height=480', '--input-rate=60'])
output=jetson.utils.videoOutput("rtp://192.168.108.102:5800",argv=['--headless']) # роутер MTS (TP-LINK) стрим
display = jetson.utils.videoOutput("video14.mp4",argv=['--headless']) # раскомменировать для  записи на диск


# функция создания маски цвета

def create_mask(frame, color):
    hsv = cv2.cvtColor(frame, cv2.COLOR_BGR2HSV)
    mask = cv2.inRange(hsv, np.array(color[0]), np.array(color[1]))
    # print("make mask",color)
    return mask

# функция поиска кубика на экране

def find_cub(frame):

    global area_porog,area_max
    y_prev=0
    color = Green
    x_green_cub = None
    y_green_cub = None 
    area_green_cub = None 
    h_green_cub=0

    
    Mask=create_mask(frame, color)
    
    contours, hierarchy = cv2.findContours(Mask, cv2.RETR_TREE, cv2.CHAIN_APPROX_SIMPLE) # на отфильтрованной маске выделяем контуры
    
    for contour in contours: # перебираем все найденные контуры
        x, y, w, h = cv2.boundingRect(contour) # Создаем прямоугольник вокруг контура
        area = cv2.contourArea(contour) # вычисляем площадь найденного контура
        #print(area)
        if area > area_porog and y>50: 
            if y_prev<y+h:
                y_prev=y+h
                h_green_cub=h
                x_green_cub = int(x + w/2)    
                y_green_cub = int(y + h/2)
                area_green_cub = area
                area_max=max(area_max,area)
                if area>area_porog: area_porog=area
                cv2.rectangle(frame, (x, y), (x + w, y + h), green_cub_color, 2)
                cv2.putText(frame, str(round(area, 1)), (x + w, y+h+10),cv2.FONT_HERSHEY_SIMPLEX, 0.5, cub_text_color, 2)
                cv2.putText(frame, str(x_green_cub)+ " " +str(y_green_cub), (x + w, y+h+25),cv2.FONT_HERSHEY_SIMPLEX, 0.5, cub_text_color, 2)
                frame=cv2.line(frame,(x_green_cub-10,y_green_cub),(x_green_cub+10,y_green_cub),(0,0,0),2)
                frame=cv2.line(frame,(x_green_cub,y_green_cub-10),(x_green_cub,y_green_cub+10),(0,0,0),2)
                frame=cv2.line(frame,(320,480),(x_green_cub,y_green_cub),green_cub_color,2)

    color = Red_up  
    x_red_cub = None 
    y_red_cub = None 
    area_red_cub = None 
    h_red_cub=0
    Mask=create_mask(frame, color)
    Mask2=create_mask(frame, Red_down)
    Mask=cv2.add(Mask,Mask2)
    contours, hierarchy = cv2.findContours(Mask, cv2.RETR_TREE, cv2.CHAIN_APPROX_SIMPLE) # на отфильтрованной маске выделяем контуры
    
    for contour in contours: # перебираем все найденные контуры
        x, y, w, h = cv2.boundingRect(contour) # Создаем прямоугольник вокруг контура
        area = cv2.contourArea(contour) # вычисляем площадь найденного контура
        if area > area_porog and y>50:
            if y_prev<y+h:
                y_prev=y+h
                h_red_cub=h
                x_red_cub = int(x + w/2)
                y_red_cub = int(y + h/2)
                area_red_cub = area
                if area>area_porog: area_porog=area
                area_max=max(area_max,area)
                cv2.rectangle(frame, (x, y), (x + w, y + h), red_cub_color, 2)
                cv2.putText(frame, str(round(area, 1)), (x + w, y+h+10),cv2.FONT_HERSHEY_SIMPLEX, 0.5, cub_text_color, 2)
                cv2.putText(frame, str(x_red_cub)+ " " +str(y_red_cub), (x + w, y+h+25),cv2.FONT_HERSHEY_SIMPLEX, 0.5, cub_text_color, 2)
                frame=cv2.line(frame,(x_red_cub-10,y_red_cub),(x_red_cub+10,y_red_cub),(0,0,0),2)
                frame=cv2.line(frame,(x_red_cub,y_red_cub-10),(x_red_cub,y_red_cub+10),(0,0,0),2)
                frame=cv2.line(frame,(320,480),(x_red_cub,y_red_cub+10),red_cub_color,2)
                   
             
 
    return x_red_cub, y_red_cub, area_red_cub, h_red_cub, x_green_cub, y_green_cub, area_green_cub, h_green_cub  

# функция поиска стартовой линии

def find_line(color):
    x1, y1 = 320 - 150, 0
    x2, y2 = 320 + 150, 100
    frame_roi = frame_line[y1:y2, x1:x2] # вырезаем часть изображение
    cv2.rectangle(frame_line, (x1, y1), (x2, y2), (0, 255, 255), 2) # рисуем прямоугольник на изображении
    mask = create_mask(frame_roi, color) # применяем маску для проверки
    contours, hierarchy = cv2.findContours(mask, cv2.RETR_TREE, cv2.CHAIN_APPROX_NONE) # на отфильтрованной маске выделяем контуры
    for contour in contours: # перебираем все найденные контуры
        x, y, w, h = cv2.boundingRect(contour) # Создаем прямоугольник вокруг контура
        area = cv2.contourArea(contour) # вычисляем площадь найденного контура
        if area > 50:
            cv2.rectangle(frame_line, (x1+x, y1+y), (x1+x+w, y1+y+h), (255, 0, 0), 2)
            return True
    return False

# функция ограничения диапазонов

def clamp(n, minn, maxn):  
    return max(min(maxn, n), minn)

# регулятор для движения согласну курсу BNO085

def bnoreg(kp,kd):
    global direction,lasterror,servocenter,clamplow,clamphigh,clock
    raw_error=angle.read()-direction+(0.25*counter*clock)
    if abs(raw_error)<180: err=raw_error
    else:
        if raw_error<0: err=raw_error%180
        else: err=raw_error%180-180

    Upr = kp*err+kd*(err-lasterror)
    lasterror = err
    servoangle = servocenter-Upr
    servoangle = clamp(servoangle, clamplow, clamphigh)  
    servokit.servo[0].angle = servoangle  

# функция нахождения координат вектора

def make_vector(p1, p2):
    return p2[0] - p1[0], p2[1] - p1[1]

# функции преобразования cuda img в opencv img, convertcolor, и обратно

def cuda_to_cv(source):
    global img
    img = source.Capture()
    bgr_img=jetson.utils.cudaAllocMapped(width=img.width,height=img.height,
    format='bgr8')
    jetson.utils.cudaConvertColor(img,bgr_img)
    #print (bgr_img)
    jetson.utils.cudaDeviceSynchronize()
    cv_img=jetson.utils.cudaToNumpy(bgr_img)
    return cv_img
def cv_to_cuda(source):
    #global frame 
    bgr_img = jetson.utils.cudaFromNumpy(source, isBGR=True)
    rgb_img = jetson.utils.cudaAllocMapped(width=bgr_img.width,height=bgr_img.height,format='rgb8')
    jetson.utils.cudaConvertColor(bgr_img, rgb_img)
    return rgb_img

# функции вывода заряда батареи и телеметрии на экран

def put_battery():
    global y_0
    bus_voltage = ina219.getBusVoltage_V()             # voltage on V- (load side)
    shunt_voltage = ina219.getShuntVoltage_mV() / 1000 # voltage between V+ and V- across the shunt
    current = ina219.getCurrent_mA()                   # current in mA
    power = ina219.getPower_W()                        # power in W
    p = (bus_voltage - 6)/2.4*100
    if(p > 100):p = 100
    if(p < 0):p = 0

    cv2.putText(frame,"Percent: "+str(round(p,2))+"%"  ,(550, y_max-10),cv2.FONT_HERSHEY_SIMPLEX, 0.25, green_cub_color, 1)
    cv2.putText(frame,"Power: "+str(round(power,2))+"W"  ,(550, y_max-20),cv2.FONT_HERSHEY_SIMPLEX, 0.25, green_cub_color, 1)
    cv2.putText(frame,"Current: "+str(round(current/1000,2))+"A"  ,(550, y_max-30),cv2.FONT_HERSHEY_SIMPLEX, 0.25, green_cub_color, 1)
    cv2.putText(frame,"Load Voltage: "+str(round(bus_voltage,2))+"V"  ,(550, y_max-40),cv2.FONT_HERSHEY_SIMPLEX, 0.25, green_cub_color, 1)
    #cv2.putText(frame,"Shunt Voltage: "+str(round(shunt_voltage,2))+"V"  ,(550, y_max-50),cv2.FONT_HERSHEY_SIMPLEX, 0.25, green_cub_color, 1)
    #cv2.putText(frame,"PSU Voltage: "+str(round(bus_voltage + shunt_voltage,2))+"V"  ,(550, y_max-60),cv2.FONT_HERSHEY_SIMPLEX, 0.25, green_cub_color, 1)
def put_telemetry():
    global x_red_cub, y_red_cub, area_red_cub, x_green_cub, y_green_cub, area_green_cub, angle_cub,direction,state,servoangle,h_red_cub,h_green_cub,angle_cub_calc,timer_cub,area_porog,clamplow, timer_mid, k_h, h_true_green, h_true_red
    cv2.putText(frame,'r_a: '+str(area_red_cub)+' x_red: '+str(x_red_cub)+' y_red: '+str(y_red_cub)+' h_red: '+str(h_red_cub),(0, y_max-470),cv2.FONT_HERSHEY_SIMPLEX, 0.5, green_cub_color, 2)
    cv2.putText(frame,'g_a: '+str(area_green_cub)+' x_gr: '+str(x_green_cub)+' y_gr: '+str(y_green_cub)+' h_green: '+str(h_green_cub),(0, y_max-450),cv2.FONT_HERSHEY_SIMPLEX, 0.5, green_cub_color, 2)
    cv2.putText(frame,'d_angle: '+str(angle_cub)+'/'+str(angle_cub_calc_red)+'/'+str(angle_cub_calc_green),(0, y_max-430),cv2.FONT_HERSHEY_SIMPLEX, 0.5, green_cub_color, 2)
    cv2.putText(frame,'BNO: '+str(angle.read()),(0, y_max-410),cv2.FONT_HERSHEY_SIMPLEX, 0.5, green_cub_color, 2)
    cv2.putText(frame,'direction: '+str(direction),(0, y_max-390),cv2.FONT_HERSHEY_SIMPLEX, 0.5, green_cub_color, 2)
    cv2.putText(frame,'state: '+str(state),(0, y_max-370),cv2.FONT_HERSHEY_SIMPLEX, 0.5, green_cub_color, 2)
    cv2.putText(frame,'servo: '+str(time.perf_counter()-timer_mid),(0, y_max-350),cv2.FONT_HERSHEY_SIMPLEX, 0.5, green_cub_color, 2)
    cv2.putText(frame,'tm: '+str(t_manevra),(0, y_max-330),cv2.FONT_HERSHEY_SIMPLEX, 0.5, green_cub_color, 2)
    cv2.putText(frame,'htrue: '+str(h_true_green)+'/'+str(h_true_red),(0, y_max-310),cv2.FONT_HERSHEY_SIMPLEX, 0.5, green_cub_color, 2)

# функия pd регулятора по x координате кубика

def pd(err):
    global kp,kd,lasterror,servocenter,servoangle,clamphigh,clamplow
    Upr = kp*err+kd*(err-lasterror)
    lasterror = err
    servoangle = servocenter+Upr+Upr*kp
    servoangle = clamp(servoangle, clamplow, clamphigh)  
    servokit.servo[0].angle = servoangle 

# функция рассчета угла отклонения кубика

def calc_cub_angle():
    global angle_cub, direction, x_red_cub, x_green_cub, mn, angle_cub_calc_red,angle_cub_calc_green, mn, clock
    angle_cub_calc_red=0
    angle_cub_calc_green=0
    if area_green_cub:
        a=[320,480]
        b=[x_green_cub,y_green_cub]
        c=[320,y_green_cub]
        vector_1 = make_vector(a, b)
        vector_2 = make_vector(a, c)
        unit_vector_1 = vector_1 / np.linalg.norm(vector_1)
        unit_vector_2 = vector_2 / np.linalg.norm(vector_2)
        dot_product = np.dot(unit_vector_1, unit_vector_2)
        angle_cub_calc_green = int(np.arccos(dot_product)*(180/np.pi))
        if clock==1:
            if x_green_cub>=320: mn=0.8
            else: mn=-0.9
            angle_cub_calc_green=(angle_cub_calc_green-angle.read()+direction)*mn
        if clock==-1:
            if x_green_cub>=320: mn=1
            else: mn=-1   
            angle_cub_calc_green=(angle_cub_calc_green+angle.read()-direction)*mn
    if area_red_cub:
        a=[320,480]
        b=[x_red_cub,y_red_cub]
        c=[320,y_red_cub]
        vector_1 = make_vector(a, b)
        vector_2 = make_vector(a, c)
        unit_vector_1 = vector_1 / np.linalg.norm(vector_1)
        unit_vector_2 = vector_2 / np.linalg.norm(vector_2)
        dot_product = np.dot(unit_vector_1, unit_vector_2)
        angle_cub_calc_red = int(np.arccos(dot_product)*(180/np.pi))
        if clock==1:
            if x_red_cub>=320: mn=-0.95
            else: mn=1   
            angle_cub_calc_red=(angle_cub_calc_red-angle.read()+direction)*mn
        if clock==-1:
            if x_red_cub>=320: mn=-1
            else: mn=1.15
            angle_cub_calc_red=(angle_cub_calc_red+angle.read()-direction)*mn

# функция подсчета кубиков     

def calccub():
    global counter,redcntr,greencntr
    if counter<=4:
        if area_green_cub is not None:greencntr+=1
        if area_red_cub is not None:redcntr+=1


# задаем значения необходимых переменных


red_cub_color=(0, 0, 255)
green_cub_color=(0,255,0)
cub_text_color=(0,255,0)#(250,50,255)
info_text_color=(255,255,0)
y_max=480


Green=([47, 81, 74], [95, 255, 255])
Red_up=[[0, 179, 100], [9, 240, 255]]
Red_down=[[150,179,100], [179,240,255]]
Orange=([0, 105, 106], [25, 175, 166])
Blue=([99, 117, 73], [135, 255, 255])
Black=([0, 0, 0], [180, 255, 89])


sch=0
angle_cub=None
servocenter=80
clamplow=5
clamphigh=170
servoangle=80
servokit.servo[0].angle = servocenter
state=-1
direction=45 
counter=0
lasterror=0
clock=1
flag_alfa=0
timer_mid=0
delay=0.4
timer_cub=0
t_manevra=0
mn=1
angle_cub_calc=0
complete_red=False
area_porog=700
area_max=0
angle_cub_calc_red=0
angle_cub_calc_green=0
mn=0
cub_color=0
direction_prev=0
k_h=1
h_true_red=0
h_true_green=0
redcntr=0
greencntr=0

# сбрасываем таймеры,стартуем поток BNO
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

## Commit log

2022-06-27 Create отдельные компоненты
2022-07-02 Rename Командные фото/readme.md to team_photo/readme.md
2022-07-02 Rename Фото автомобиля/readme.md to robot_photo/readme.md
2022-07-02 Rename Схематические диаграммы/readme.md to schematic/readme.md
